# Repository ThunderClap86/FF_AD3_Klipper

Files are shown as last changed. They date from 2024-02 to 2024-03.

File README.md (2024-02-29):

# FlashForge Adventure 3 - Klipper + BTT SKR Pico / Raspberry Pi Zero 2W Upgrade  *Updates to this repo are in-progress*

<p align="center">
  <a>
    Klippventurer logo
  </a>
</p>

Warning: this Upgrade is a Major effort and is recomended for *Advanced* 3D print users with some electronics/soldering skills only. If you would like to keep your OEM mainboard and wiring, please see the Klippventure project by VioSynthax.

# 3D Printed items
are available via Printables:

https://www.printables.com/model/437968-flashforge-adventurer-3-klipper-revo-6-bltouch-btt

# Required Components:
* BigTreeTech SKR Pico
* Raspberry Pi Zero 2w (DO NOT attempt to use an older/weaker Pi Zero model)
* PCB's: AD3 HE and AD3 HE BreakOut Boards.
* E3D Revo 6 or E3D V6 hotend. 
* Good Quality Ribbon cable - 20 conductor - ~1.5 meters/ 5 feet.
* 2x9 *OR* 2x10 Pin IDC Cable Connectors and sockets. *PCB design intended for 2x9, for convenience the 2x10 fits fine if aligned properly. 
* 2x Molex, Micro-Fit 3.0, 43650, 2 Way, 1 Row, Right Angle PCB Headers
* Assorted JST-PH PCB Sockets and Cable Connectors
* 2x PCB Mount Screw Terminal Blocks eg CUI Devices TB004-508-02BE
* 24v to 5v buck converter to power your Raspberry Pi **Not necessary in UART mode between Pi and Pico. 
* Printed Parts

# UPDATES:
* 20 Feb 2024:
  -Added to original to allow for SKR Pico and Pi Zero combination.
  -Added method of Y-belt tightening without cutting belt.
  -Updated bed heat soldering options.
  -Added STL for Hotend PCB cover with FlashForge logo.
  -Addes STL for CR-Touch probe mounting
  -Updated printer.cfg file for Pico. --adjusted driver current to compensate for overheating on long and hot prints, pico pinouts added, pico features refined. 
  -Added wiring/config instructions for FlashForge camera use with Klipper/Pi Zero.

* 12th April 2023 - fixed filament macros - please see the Filament_Sensor.cfg file for prerequisites  
* 2nd April 2023 - reduced max speed to 100mm/s - any higher results in layer shifts due to the temps getting too high for the stock stepper motors (at least while printing high tempmaterials like ASA)
* 1st April 2023 - Tweaks to max speed and driver current - the steppers don't seem to like travel speeds over 150mm/s without overheating and causing layer shifts
* 31st March 2023 - Printer now calibrated and Printer.cfg has been updated.
* 30th March 2023 - Everything now works! 

# Videos
FlashForge Adventurer 3 gets a new Brain, Hot-End and Klipper:
https://youtu.be/USZoIhBnA24

Sensorless Homing in Action:
https://youtu.be/0Acrmv7VkdY

and Printing ASA:
https://youtu.be/akCvX6l-e6o

# Klipper Features in use:
* Sensorless Homing
* Adaptive Purge
* Adaptive Mesh Levelling w/ BLTouch
* Auto-Load Filament using Filament Sensor
* Auto Unload Filament when run-out detected
* Unload macro for when you just want to change Filament types/colours etc
* Auto-Extraction Fan at the end of Print (via End G-Code)
* Working LED lighting

# NOTE: 
** Alternative Belt Tensioning for Y-Axis **
The plastic idler pulley mount needs to be un-bolted from the frame and remove the belt and idler pulley from the assembly. Take the plastic mount to a vise/clamp, and extend the bolt holes from a circle into the shape of a channel. This will give you approximately 2-3mm of tensioning distance. Be careful to not get too close to the edge and weaken the mount to the point of failure. I am working on designing a printed replacement part for this, but this has been a viable workaround for my variation in this build. 

The factory belt tension on this printer is too loose to exceed 1k acceleration and 100mm/s print speeds. To rectify this you need to retension the X and Y axis belts properly (tight is good, but dont over do it). The Y axis is a PITA as it can only be fixed when the printer is fully disassembled. The Y belt is a continuous loop with no tension adjuster. So you'll need to cut out roughly 5mm from the belt and re-install it as snug as you can get it. I then used some "Selly's Power Grip" to ensure the belts dont jump out of the jaws holding them.

If you still have Y axis layer shifting, I recommend replacing the motor with a better quality unit.

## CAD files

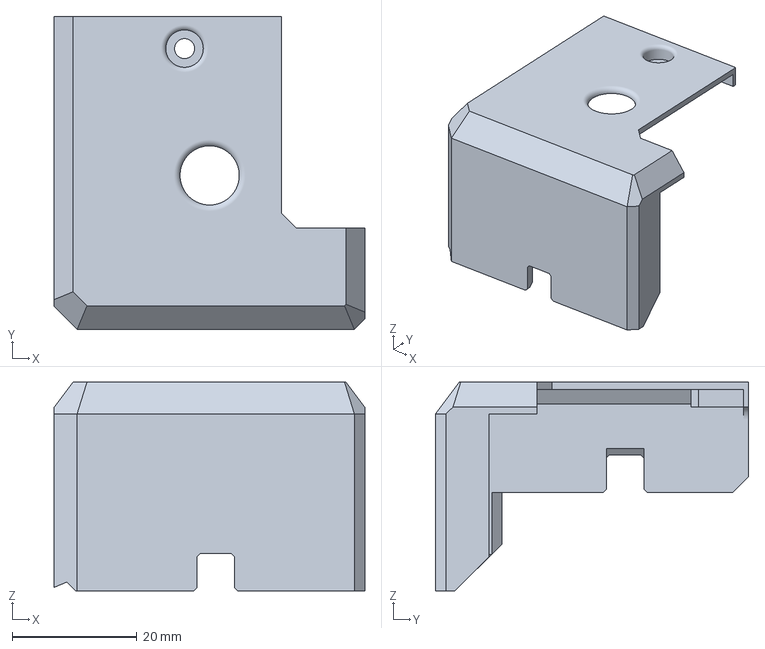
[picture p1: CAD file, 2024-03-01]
Printable Items - Pico/Logo_Lid.3mf
49.8 x 50.2 x 33.4 mm

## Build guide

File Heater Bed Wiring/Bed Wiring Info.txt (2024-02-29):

The outer most two traces are for the SMD thermistor of the heat pad. The only required action is to desolder the one resistor on its own. The rest of the traces are split
evenly, mark the inner/middle two traces and avoid soldering on them. This will avoid a short that could cause a fire. 

The SMD capacitors are fine to keep, these will smooth the heating power/current across the heat bed element.

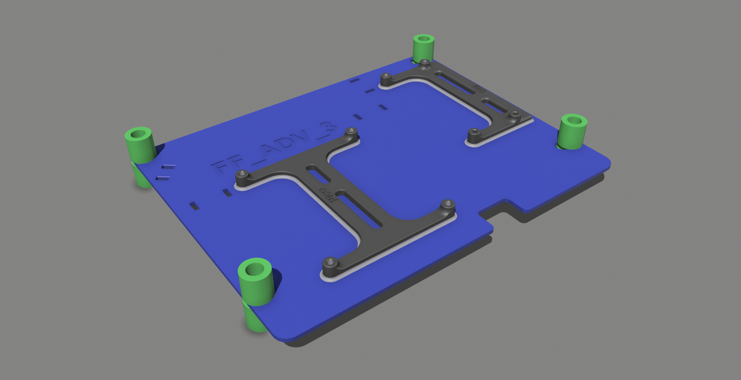
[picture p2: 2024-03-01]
Printable Items - Pico/Board_Mount_Image.png

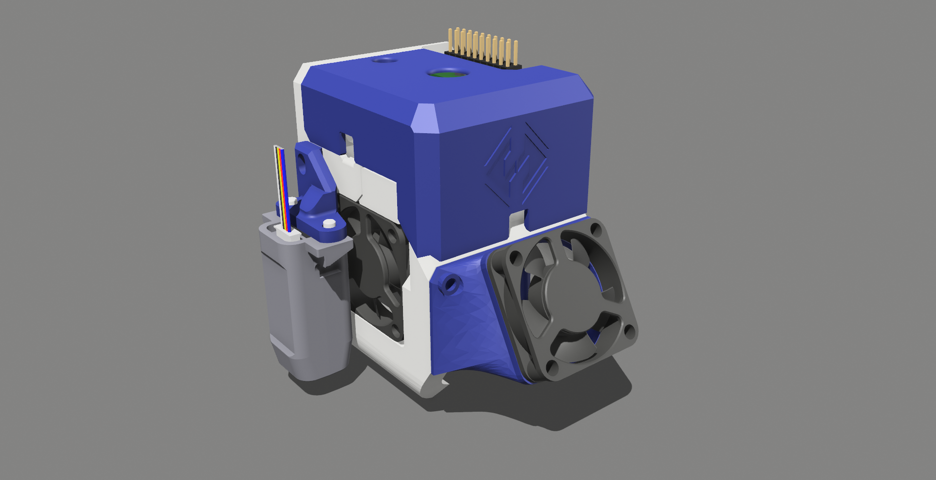
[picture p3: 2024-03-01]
Printable Items - Pico/Hotend_image.png

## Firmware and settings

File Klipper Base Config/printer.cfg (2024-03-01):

# This file contains common pin mappings for the BIGTREETECH SKR Pico V1.0
# To use this config, the firmware should be compiled for the RP2040 with
# UART for the KlipperVenturer conversion communication.

# The "make flash" command does not work on the SKR Pico V1.0. Instead,
# after running "make", copy the generated "out/klipper.uf2" file
# to the mass storage device in RP2040 boot mode

# See docs/Config_Reference.md for a description of parameters.

[include Adaptive_Mesh.cfg]
[include Adaptive_Purge.cfg]
[include macros.cfg] 
[include probe_bltouch.cfg]
[include mainsail.cfg]
[include Filament_Sensor.cfg]

[printer]
kinematics: cartesian
max_velocity: 150
max_accel: 3000
max_accel_to_decel: 3000
max_z_accel: 25
square_corner_velocity: 5

[stepper_x]
step_pin: gpio11
dir_pin: !gpio10
enable_pin: !gpio12
microsteps: 16
rotation_distance: 33.36
endstop_pin: tmc2209_stepper_x:virtual_endstop #^gpio4 for pico pin. 
homing_retract_dist: 0
homing_speed: 25
position_endstop: 0
position_max: 160 #IMPORTANT 160 is too large on purpose. Refine this carefully after your build is complete. Should be near 154-156 when completed. 


[tmc2209 stepper_x]
uart_pin: gpio9
tx_pin: gpio8
uart_address: 0
run_current: 0.650
stealthchop_threshold: 999999
diag_pin: ^PC0      # Set to MCU pin connected to TMC DIAG pin
driver_SGTHRS: 75  # 255 is most sensitive value, 0 is least sensitive


[stepper_y]
step_pin: gpio6
dir_pin: !gpio5
enable_pin: !gpio7
microsteps: 16
rotation_distance: 33.38
endstop_pin: tmc2209_stepper_y:virtual_endstop #^gpio3 pico pin
homing_retract_dist: 0
homing_speed: 25
position_endstop: 0
position_max: 155 #IMPORTANT 155 is too large on purpose. Refine this carefully after your build is complete. 
#Should be near 147-153 when completed.


[tmc2209 stepper_y]
uart_pin: gpio9
tx_pin: gpio8
uart_address: 2
run_current: 0.650
stealthchop_threshold: 999999
diag_pin: ^PC1      # Set to MCU pin connected to TMC DIAG pin
driver_SGTHRS: 75  # 255 is most sensitive value, 0 is least sensitive


[stepper_z]
step_pin: gpio19
dir_pin: gpio28
enable_pin: !gpio2
microsteps: 16
rotation_distance: 6.25
# endstop_pin: PC2
endstop_pin: probe:z_virtual_endstop #^gpio25 pico pin.
# position_endstop: 0
position_max: 150
homing_speed: 20
second_homing_speed: 15
homing_retract_dist: 7

[tmc2209 stepper_z]
uart_pin: gpio9
tx_pin: gpio8
uart_address: 1
run_current: 0.580
stealthchop_threshold: 999999


[extruder]
step_pin: gpio14
dir_pin: !gpio13
enable_pin: !gpio15
microsteps: 16
rotation_distance: 33.500
nozzle_diameter: 0.400
filament_diameter: 1.750
heater_pin: gpio23
sensor_type: ATC Semitec 104NT-4-R025H42G 
sensor_pin: gpio27gpio27
min_temp: 0
max_temp: 300
min_extrude_temp: 180
max_extrude_only_distance: 900
max_extrude_only_velocity: 120
max_extrude_only_accel: 1000
min_extrude_temp: 180
max_extrude_cross_section: 5
pressure_advance: 0.050
# pressure_advance_smooth_time: 0.04

[tmc2209 extruder]
uart_pin: PC11
tx_pin: PC10
interpolate: True
uart_address: 3
run_current: 1.3
stealthchop_threshold: 0


[heater_bed]
heater_pin: PC9
sensor_type: Generic 3950
sensor_pin: PA0
min_temp: 0
max_temp: 120


[idle_timeout]
gcode:
  PANEL_BEEP   
  M84 ; disable motors
  TURN_OFF_HEATERS
  SET_PIN PIN=led_lights VALUE=0.00
  M117 Ready
timeout: 3600

[bltouch]
x_offset: -13.25
y_offset: 10.0
#z_offset: 5.0

[heater_fan hotend_fan]
#Heatbreak Cooling Fan
pin: PC6
heater: extruder
heater_temp: 50.0

[fan_generic exhaust_fan]
#Chamber Cooling Fan
pin: PB15


[fan]
#Part Cooling Fan
pin: PC7

[mcu]
serial: /dev/serial/by-id/usb-Klipper_stm32g0b1xx_5200320007504B5735313920-if00

[mcu rpi]
serial: /tmp/klipper_host_mcu


[output_pin led_lights]
pin: PA8
value: 1

[gcode_arcs]
resolution: 1.0

[force_move]
enable_force_move: True
#   Set to true to enable FORCE_MOVE and SET_KINEMATIC_POSITION
#   extended G-Code commands. The default is false.

[exclude_object]

[skew_correction]

[display_status]

[pause_resume]

[display]
lcd_type: emulated_st7920
en_pin: EXP1_7
spi_software_sclk_pin: EXP1_6
spi_software_mosi_pin: EXP1_8
spi_software_miso_pin: PA3
encoder_pins: ^EXP1_5, ^EXP1_3
click_pin: ^!EXP1_2

[temperature_sensor raspberry_pi]
sensor_type: temperature_host
min_temp: 10
max_temp: 100


[temperature_sensor mcu_temp]
sensor_type: temperature_mcu
min_temp: 0
max_temp: 100

[output_pin BEEPER_pin]
pin: EXP1_1
#   Beeper pin. This parameter must be provided.
pwm: True
#   A piezo beeper needs a PWM signal, a DC buzzer doesn't.
value: 0
#   Silent at power on, set to 1 if active low.
shutdown_value: 0
#   Disable at emergency shutdown (no PWM would be available anyway).
cycle_time: 0.001
#   Default PWM frequency : 0.001 = 1ms will give a tone of 1kHz
#   Although not pitch perfect.

[respond]
default_type: echo
#   Sets the default prefix of the "M118" and "RESPOND" output to one
#   of the following:
#       echo: "echo: " (This is the default)
#       command: "// "
#       error: "!! "
default_prefix: echo:
#   Directly sets the default prefix. If present, this value will
#   override the "default_type".

[menu __main __octoprint]
type: disabled

[board_pins]
aliases:
    # EXP1 header
    EXP1_1=PB5,  EXP1_3=PA9,   EXP1_5=PA10, EXP1_7=PB8, EXP1_9=<GND>,
    EXP1_2=PA15, EXP1_4=<RST>, EXP1_6=PB9,  EXP1_8=PD6, EXP1_10=<5V>

# See the sample-lcd.cfg file for definitions of common LCD displays.

#*# <---------------------- SAVE_CONFIG ---------------------->
#*# DO NOT EDIT THIS BLOCK OR BELOW. The contents are auto-generated.
#*#
#*# [extruder]
#*# control = pid
#*# pid_kp = 35.959
#*# pid_ki = 4.795
#*# pid_kd = 67.424
#*#
#*# [heater_bed]
#*# control = pid
#*# pid_kp = 61.177
#*# pid_ki = 0.917
#*# pid_kd = 1020.890
#*#
#*# [bed_mesh default]
#*# version = 1
#*# points =
#*# 	  -0.302734, 0.066406, 0.224609, 0.111328
#*# 	  -0.265625, -0.039062, 0.021484, -0.023438
#*# 	  -0.283203, -0.080078, -0.031250, -0.101562
#*# tension = 0.2
#*# min_x = 21.03
#*# algo = lagrange
#*# y_count = 3
#*# mesh_y_pps = 2
#*# min_y = 39.519999999999996
#*# x_count = 4
#*# max_y = 108.46
#*# mesh_x_pps = 2
#*# max_x = 128.97
#*#
#*# [bltouch]
#*# z_offset = 2.443
#*#
#*# [skew_correction my_skew_profile]
#*# xy_skew = -0.0008904302644857634
#*# xz_skew = 0.0
#*# yz_skew = 0.0

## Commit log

2024-02-29 Updated Bed Wiring Info.txt
2024-02-29 Create Printable Items
    STL's for the modifications to the ADV3
2024-03-01 Create Print Files
2024-03-01 Update Print Files
2024-03-01 Rename Print Files to Print Settings
